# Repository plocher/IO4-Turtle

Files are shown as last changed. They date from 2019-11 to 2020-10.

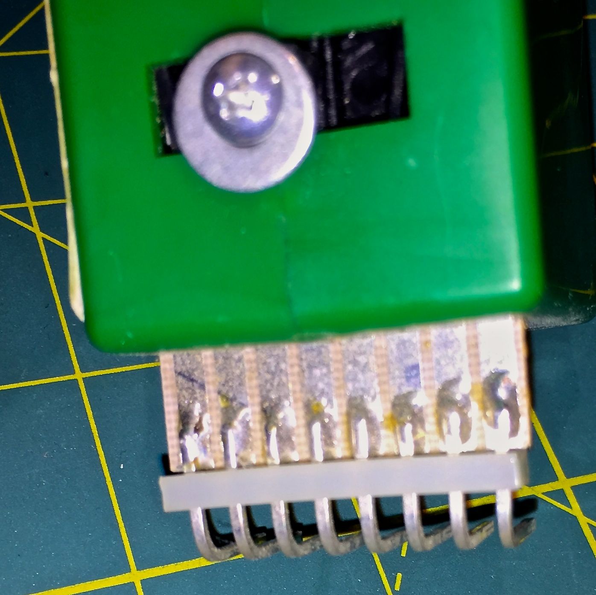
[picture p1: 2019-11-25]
Molex-on-Tortoise-2.jpg

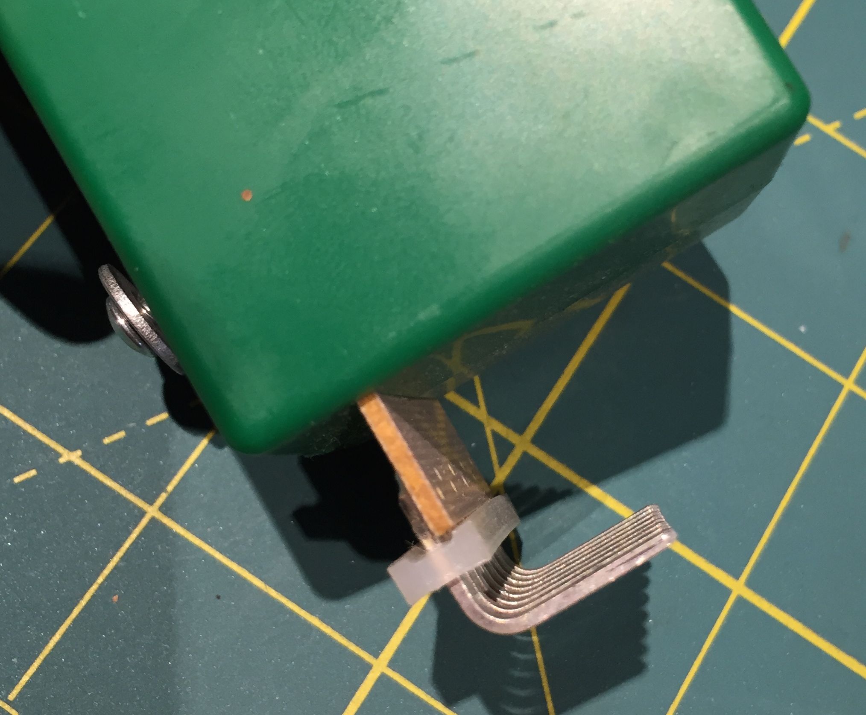
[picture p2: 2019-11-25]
Molex-on-Tortoise-3.jpg

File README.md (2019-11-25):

# IO4-Turtle
## License: CERN Open Hardware Licence v1.2

IO4 Tortoise driver with occupancy and point position feedback

Carrier board, DFM, feedback LEDS that don't pass tortoise current and
field changable N/R positioning, feedback and frog selection.

This is an adaptation of my older PIC-based ExpressPCB Turtle
project, which is why the version numbers start at 4….  It has
evolved quite a bit, in form factor and functionality as it has
been used on my layout.

This board mounts on a Tortoise via a sweat-soldered right angle
Molex M-M connector, plugs into an [IOB-Turtle](/pages/IOB-Turtle)
or other IO4 compatible port.

The Tortoise provides:

 * OS section occupancy (so you don't throw a turnout out from under a train...),
 * Turnout point position feedback (Normal, in transit, Diverging)
 * easy frog polarity changes for dealing with wiring mishaps
 * easy Normal/Reverse changes for when the Normal route thru a turnout needs to go the other way.
 * Tortoise motor debouncing when it reaches the end of travel
 * feedback LEDs to show Occupancy (yellow) and commanded position (red/green)

It uses my standard IO4 RJ12/6 wiring interface:

 * pin 1: 9-12vDC
 * pin 2: !DIVERGING - Turnout Position Feedback - low = Diverging, high = not diverging
 * pin 3: !NORMAL    - Turnout Position Feedback - low = Normal, high = not normal
 * pin 4: !OCCUPIED  - Detector Feedback - low = occupied, high = empty
 * pin 5: !MOTOR     - Motor Control Input - Low = Normal, High = Diverging
 * pin 6: GND

It also connects to the local DCC track power feed and to the turnout's isolated-for-detection-purposes stock and frog rails.

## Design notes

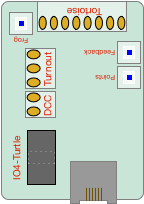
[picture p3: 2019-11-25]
IO4-Turtle-Graphic.png

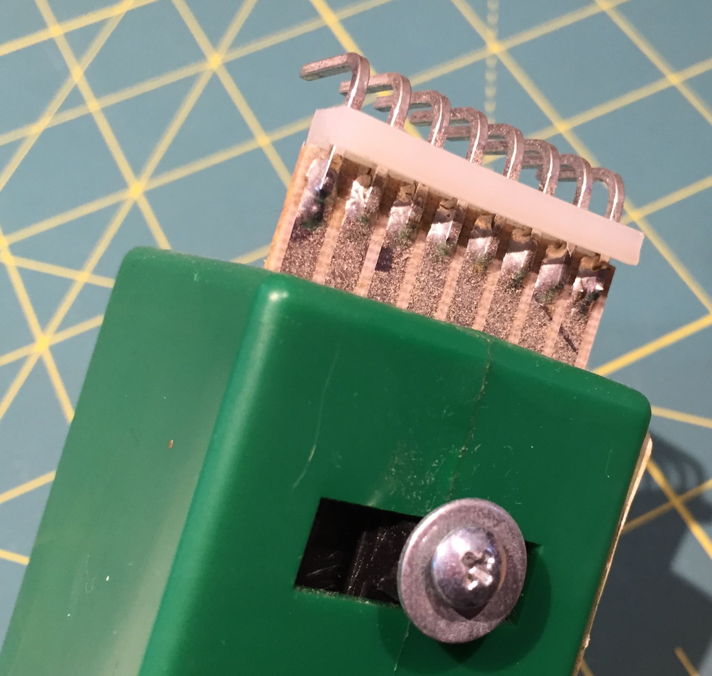
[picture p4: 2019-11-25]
Molex-on-Tortoise-1.jpg

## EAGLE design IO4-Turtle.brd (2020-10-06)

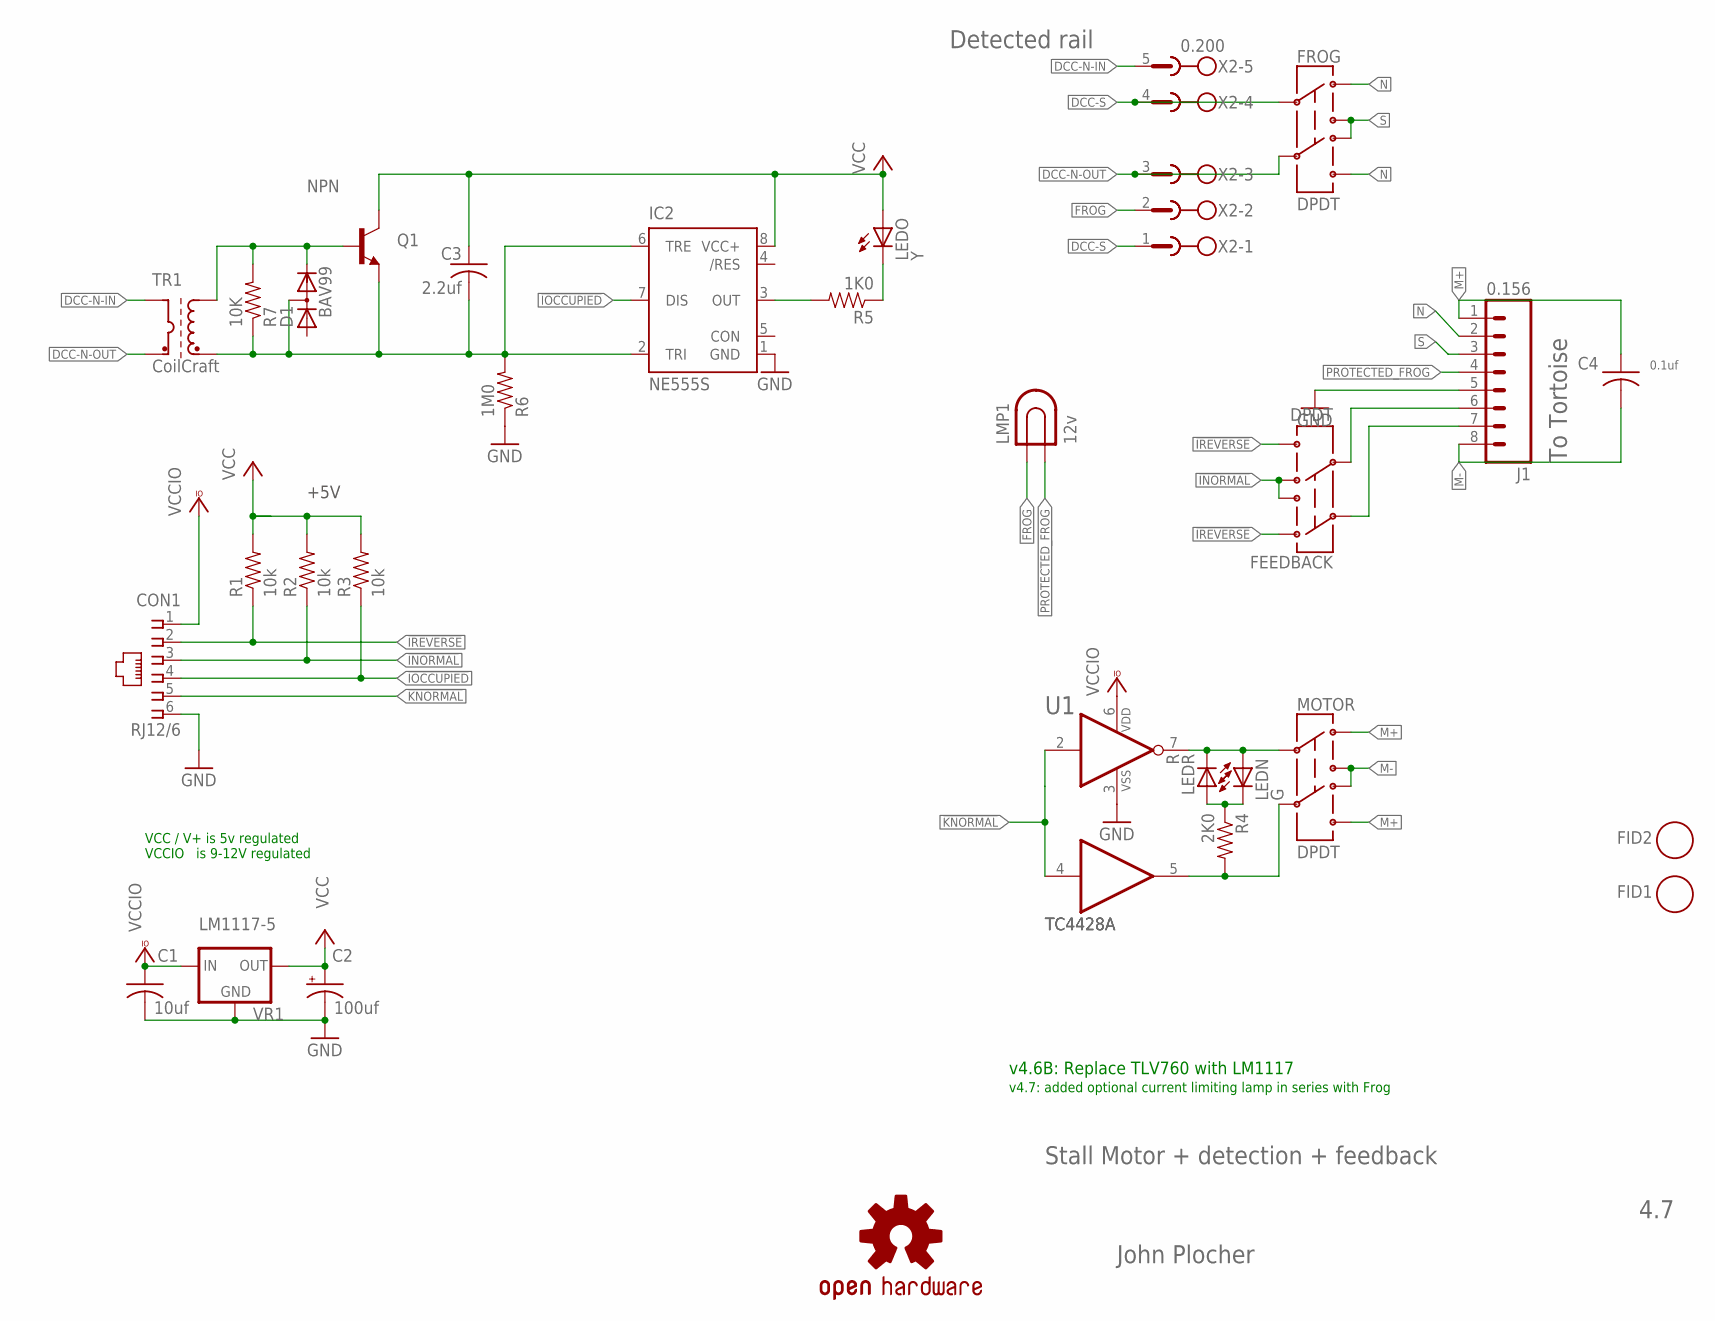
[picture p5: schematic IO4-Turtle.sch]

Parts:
C1: 10uf; 0603-CAP
C2: 100uf; PANASONIC_D
C3: 2.2uf; 0603-CAP
C4: 0.1uf; 0805-CAP
CON1: RJ12/6; RJ25-INVERTED
D1: BAV99; SOT23
FEEDBACK: DPDT; 8X8-SQ-PB
FID1, FID2: FIDUCIAL; FIDUCIAL_1MM
FROG: DPDT; 8X8-SQ-PB
IC1: TC4428A; SO-08
IC2: NE555S; SO08
J1: 0.156; KK-156-8-F
LEDN: G; 0603-LED
LEDO: Y; 0603-LED
LEDR: R; 0603-LED
LMP1: 12v; BULB-3156
MOTOR: DPDT; 8X8-SQ-PB
OSHW1: OSHW; OSHW-LOGO-M
Q1: NPN; SOT23
R1, R2, R3: 10k; 0603-RES
R4: 2K0; 0603-RES
R5: 1K0; 0603-RES
R6: 1M0; 0603-RES
R7: 10K; 0603-RES
TR1: CoilCraft; TH-T4
VR1: LM1117-5; SOT223
X2: 0.200; MSTBA5

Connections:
!INORMAL: CON1.3, FEEDBACK.1B, FEEDBACK.2A, R2.1
!IOCCUPIED: CON1.4, IC2.7 (DIS), R3.1
!IREVERSE: CON1.2, FEEDBACK.1A, FEEDBACK.2B, R1.1
!KNORMAL: CON1.5, IC1.2 (I), IC1.4 (I)
+12V: C1.1, CON1.1, IC1.6 (VDD), VR1.3 (IN)
DCC-N-IN: TR1.P1 (DCC-A), X2.5
DCC-N-OUT: FROG.2C, TR1.P2 (DCC-B), X2.3
DCC-S: FROG.1C, X2.1, X2.4
FROG: LMP1.P$1 (1), X2.2
GND: C1.2, C2.-, CON1.6, IC1.3 (VSS), IC2.1 (GND), J1.5, R6.1, VR1.1 (GND)
M+: C4.1, J1.1, MOTOR.1A, MOTOR.2B
M-: C4.2, J1.8, MOTOR.1B, MOTOR.2A
N: FROG.1A, FROG.2B, J1.2
unnamed: IC1.7 (O), LEDN.A, LEDR.C, MOTOR.1C
unnamed: D1.2 (C), Q1.1 (B), R7.2, TR1.S1 (OUT-A)
unnamed: LEDN.C, LEDR.A, R4.1
unnamed: LEDO.C, R5.1
unnamed: IC2.3 (OUT), R5.2
unnamed: FEEDBACK.2C, J1.6
unnamed: FEEDBACK.1C, J1.7
unnamed: IC1.5 (O), MOTOR.2C, R4.2
PROTECTED_FROG: J1.4, LMP1.P$2 (2)
S: FROG.1B, FROG.2A, J1.3
TRIGGER: C3.2, D1.3 (AC), IC2.2 (TRI), IC2.6 (TRE), Q1.2 (E), R6.2, R7.1, TR1.S2 (OUT-B)
V+: C2.+, C3.1, IC2.8 (VCC+), LEDO.A, Q1.3 (C), R1.2, R2.2, R3.2, VR1.2 (OUT), VR1.4 (OUT)

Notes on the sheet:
John Plocher
4.7
Stall Motor + detection + feedback
To Tortoise
Detected rail
v4.6B: Replace TLV760 with LM1117
+5V
v4.7: added optional current limiting lamp in series with Frog
VCC / V+ is 5v regulated VCCIO is 9-12V regulated

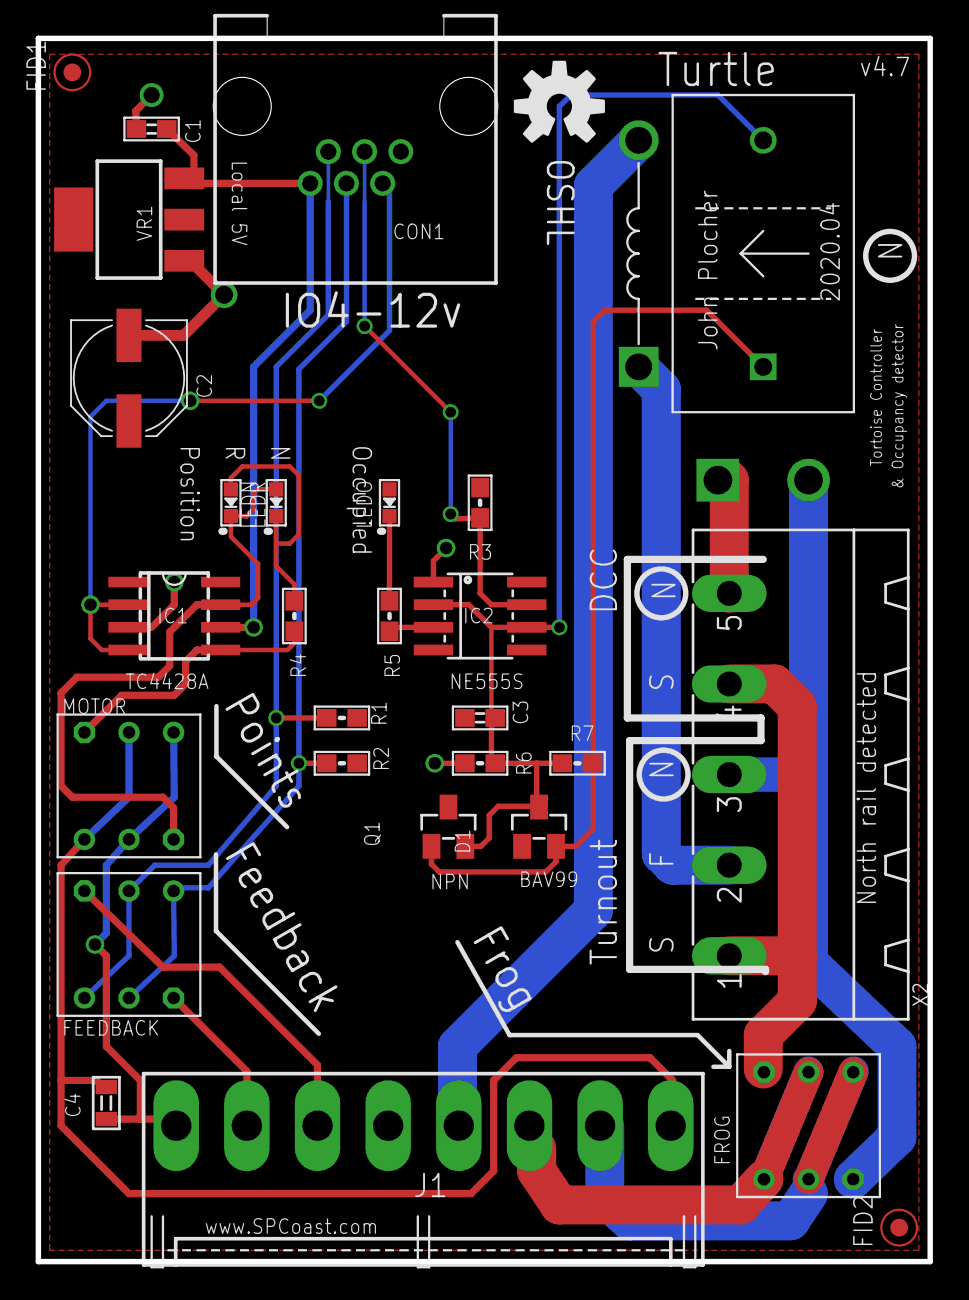
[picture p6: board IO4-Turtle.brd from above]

Board: 2 copper layers, 50.0 x 68.6 mm, 30 parts (0 on the bottom side), 25 nets.

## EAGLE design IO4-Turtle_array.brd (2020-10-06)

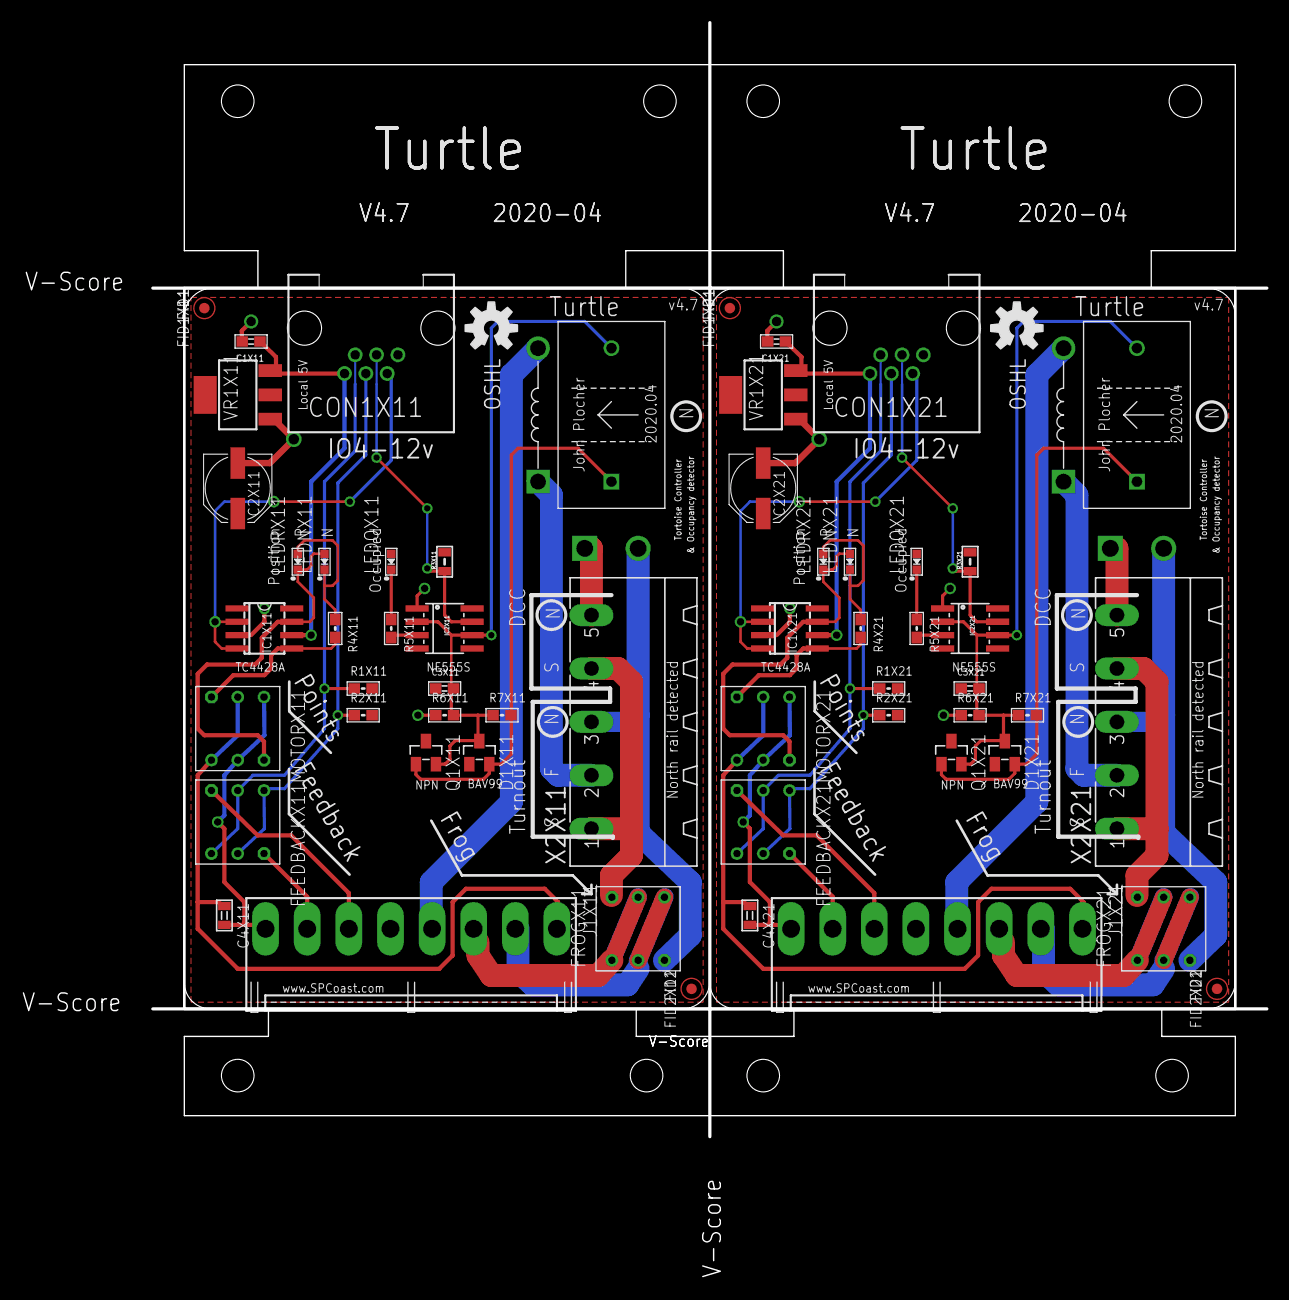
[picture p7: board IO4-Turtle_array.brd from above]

Board: 2 copper layers, 106.0 x 106.0 mm, 61 parts (0 on the bottom side), 50 nets.

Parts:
C1X11, C1X21: 10uf; 0603-CAP
C2X11, C2X21: 100uf; PANASONIC_D
C3X11, C3X21: 2.2uf; 0603-CAP
C4X11, C4X21: 0.1uf; 0805-CAP
CON1X11, CON1X21: RJ12/6; RJ25-INVERTED
D1X11, D1X21: BAV99; SOT23
FEEDBACKX11, FEEDBACKX21: DPDT; 8X8-SQ-PB
FID1X11, FID1X21, FID2X11, FID2X21: FIDUCIAL; FIDUCIAL_1MM
FROGX11, FROGX21: DPDT; 8X8-SQ-PB
IC1X11, IC1X21: TC4428A; SO-08
IC2X11, IC2X21: NE555S; SO08
J1X11, J1X21: 0.156; KK-156-8-F
LEDNX11, LEDNX21: G; 0603-LED
LEDOX11, LEDOX21: Y; 0603-LED
LEDRX11, LEDRX21: R; 0603-LED
LMP1X11, LMP1X21: 12v; BULB-3156
MOTORX11, MOTORX21: DPDT; 8X8-SQ-PB
OSHW1X11, OSHW1X21: OSHW; OSHW-LOGO-M
Q1X11, Q1X21: NPN; SOT23
R1X11, R1X21, R2X11, R2X21: 10k; 0603-RES
R3X11, R3X21: 10k; 0805-RES
R4X11, R4X21: 2K0; 0603-RES
R5X11, R5X21: 1K0; 0603-RES
R6X11, R6X21: 1M0; 0603-RES
R7X11, R7X21: 10K; 0603-RES
TR1X11, TR1X21: CoilCraft; TH-T4
VR1X11, VR1X21: LM1117-5; SOT223
X2X1: 10x10; BOARD-DINRAIL-2.7IN-5CM-DUAL
X2X11, X2X21: 0.200; MSTBA5

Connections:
!INORMALX11: CON1X11.3, FEEDBACKX11.1B, FEEDBACKX11.2A, R2X11.1
!INORMALX21: CON1X21.3, FEEDBACKX21.1B, FEEDBACKX21.2A, R2X21.1
!IOCCUPIEDX11: CON1X11.4, IC2X11.7, R3X11.1
!IOCCUPIEDX21: CON1X21.4, IC2X21.7, R3X21.1
!IREVERSEX11: CON1X11.2, FEEDBACKX11.1A, FEEDBACKX11.2B, R1X11.1
!IREVERSEX21: CON1X21.2, FEEDBACKX21.1A, FEEDBACKX21.2B, R1X21.1
!KNORMALX11: CON1X11.5, IC1X11.2, IC1X11.4
!KNORMALX21: CON1X21.5, IC1X21.2, IC1X21.4
+12VX11: C1X11.1, CON1X11.1, IC1X11.6, VR1X11.3
+12VX21: C1X21.1, CON1X21.1, IC1X21.6, VR1X21.3
DCC-N-INX11: TR1X11.P1, X2X11.5
DCC-N-INX21: TR1X21.P1, X2X21.5
DCC-N-OUTX11: FROGX11.2C, TR1X11.P2, X2X11.3
DCC-N-OUTX21: FROGX21.2C, TR1X21.P2, X2X21.3
DCC-SX11: FROGX11.1C, X2X11.1, X2X11.4
DCC-SX21: FROGX21.1C, X2X21.1, X2X21.4
FROGX11: LMP1X11.P$1, X2X11.2
FROGX21: LMP1X21.P$1, X2X21.2
GNDX11: C1X11.2, C2X11.-, CON1X11.6, IC1X11.3, IC2X11.1, J1X11.5, R6X11.1, VR1X11.1
GNDX21: C1X21.2, C2X21.-, CON1X21.6, IC1X21.3, IC2X21.1, J1X21.5, R6X21.1, VR1X21.1
M+X11: C4X11.1, J1X11.1, MOTORX11.1A, MOTORX11.2B
M+X21: C4X21.1, J1X21.1, MOTORX21.1A, MOTORX21.2B
M-X11: C4X11.2, J1X11.8, MOTORX11.1B, MOTORX11.2A
M-X21: C4X21.2, J1X21.8, MOTORX21.1B, MOTORX21.2A
unnamed: IC1X11.7, LEDNX11.A, LEDRX11.C, MOTORX11.1C
unnamed: IC1X21.7, LEDNX21.A, LEDRX21.C, MOTORX21.1C
unnamed: D1X11.2, Q1X11.1, R7X11.2, TR1X11.S1
unnamed: D1X21.2, Q1X21.1, R7X21.2, TR1X21.S1
unnamed: LEDNX11.C, LEDRX11.A, R4X11.1
unnamed: LEDNX21.C, LEDRX21.A, R4X21.1
unnamed: LEDOX11.C, R5X11.1
unnamed: LEDOX21.C, R5X21.1
unnamed: IC2X11.3, R5X11.2
unnamed: IC2X21.3, R5X21.2
unnamed: FEEDBACKX11.2C, J1X11.6
unnamed: FEEDBACKX21.2C, J1X21.6
unnamed: FEEDBACKX11.1C, J1X11.7
unnamed: FEEDBACKX21.1C, J1X21.7
unnamed: IC1X11.5, MOTORX11.2C, R4X11.2
unnamed: IC1X21.5, MOTORX21.2C, R4X21.2
NX11: FROGX11.1A, FROGX11.2B, J1X11.2
NX21: FROGX21.1A, FROGX21.2B, J1X21.2
PROTECTED_FROGX11: J1X11.4, LMP1X11.P$2
PROTECTED_FROGX21: J1X21.4, LMP1X21.P$2
SX11: FROGX11.1B, FROGX11.2A, J1X11.3
SX21: FROGX21.1B, FROGX21.2A, J1X21.3
TRIGGERX11: C3X11.2, D1X11.3, IC2X11.2, IC2X11.6, Q1X11.2, R6X11.2, R7X11.1, TR1X11.S2
TRIGGERX21: C3X21.2, D1X21.3, IC2X21.2, IC2X21.6, Q1X21.2, R6X21.2, R7X21.1, TR1X21.S2
V+X11: C2X11.+, C3X11.1, IC2X11.8, LEDOX11.A, Q1X11.3, R1X11.2, R2X11.2, R3X11.2, VR1X11.2, VR1X11.4
V+X21: C2X21.+, C3X21.1, IC2X21.8, LEDOX21.A, Q1X21.3, R1X21.2, R2X21.2, R3X21.2, VR1X21.2, VR1X21.4

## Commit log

2020-04-26 cleanup, replaced LM1117 output cap
    [IO4-Turtle.brd, IO4-Turtle.sch, IO4-Turtle_array.brd]
2020-04-26 silkscreen cleanup, better power routing
    [IO4-Turtle.brd, IO4-Turtle.sch, IO4-Turtle_array.brd]
2020-05-30 fixed panelization bug - re-added part values
    [IO4-Turtle.brd, IO4-Turtle.sch]
2020-10-05 added values for connectors
    [IO4-Turtle.brd, IO4-Turtle.sch, IO4-Turtle_array.brd]
2020-10-06 normalized values
    [IO4-Turtle.brd, IO4-Turtle.sch, IO4-Turtle_array.brd]

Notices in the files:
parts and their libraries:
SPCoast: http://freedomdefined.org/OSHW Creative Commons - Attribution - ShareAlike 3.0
